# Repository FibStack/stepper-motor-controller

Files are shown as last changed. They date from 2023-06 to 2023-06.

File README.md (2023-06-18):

# Stepper Motor Controller

## Overview

This repository includes the source files for the Stepper Motor Control board, capable of controlling the direction, steps, and speed of up to four stepper motors concurrently through the I2C interface. 

Kindly note that the project is currently in the prototype phase, and further changes and updates are expected.

## Project organization

- **hardware/** - this folder contains the board circuit schematic and PCB design files.
- **software/util** - contains the source code of a simple CLI application to interact with the board.
- **software/stepper-motor-controller** - contains the firmware source code for ATTiny devices.

## Development tools
- **[Microchip Studio 7.0](https://www.microchip.com/en-us/tools-resources/develop/microchip-studio)**: The IDE for writing and building source code for the ATTiny chip. We also use this tool to flash the chip.
- **[ATMEL-ICE](https://www.microchip.com/en-us/development-tool/ATATMEL-ICE)**: Hardware tool for flashing program and EEPROM memories.
- **GCC** compiler: To complie C utility code on Raspberry Pi.
- **[KiCad EDA](https://www.kicad.org/)**: Schematic and PCB design.

To construct the PCB, please export the gerber files according to the manufacturer's guidelines.

To build the CLI utility, navigate to the `util` folder and execute the `make` command. Please note that this works only on **Raspberry Pi OS**.

To build the ATTiny826 firmware, open the project in Microchip Studio. Build the solution to generate the `*.HEX` and `*.EEP` files. Next, use the appropriate tool available to flash the chip.

## BOM

| # | Components | Recommended models | Footprint | Quantity |
| --- | --- | --- | --- | --- |
| 1 | PCB | Recommended two-layer PCB board of 1.6 mm thickness | | 1 |
| 2 | U1 | SN74LS148 | SOIC-16, 3.9x9.9mm, pitch: 1.27mm | 1 |
| 3 | U2 | ATtiny826 | SOIC-20, 7.5x12.8mm, pitch: 1.27mm | 1 |
| 4 | C1, C4 | Any 1uF 50V SMD capacitor | 0603 (1608 metric) | 2 |
| 5 | C2 | Any 10nF 50V SMD capacitor | 0603 (1608 metric) | 1 |
| 6 | C3, C5 | Any 100nF 50V SMD capacitor | 0603 (1608 metric) | 2 |
| 7 | R1 | Any 470 - 1K 5% 1/4W SMD Resistor | 0603 (1608 metric) | 1 |
| 8 | R2-R13 | Any 10K 5% 1/4W SMD Resistor | 0603 (1608 metric) | 12 |
| 9 | Q1, Q2 | 2N7002 N-channel MOSFET transistor, 60V 300mA | SOT-23-2 | 2 |
| 10 | D1 | SMD LED RED | 0603 (1608 metric) | 1 |
| 11 | J1 | Extended GPIO Male Female Header, 2x20, pitch 2.54mm | 2x20 - P2.54mm | 1 |
| 12 | J2 | Optional, Male Header Connector, 2x3, pitch 2.54mm | 2x3 - P2.54mm | 1 |
| 13 | J3 | Any male connector, 1x2, pitch 2.54mm | 1x2 - P2.54mm | 1 |
| 14 | J4 | Male Header Connector, 2x8, pitch 2.54mm | 2x8 - P2.54mm | 1 |
| 15 | J5, J6, J7, J8 | Male Header Connector, 1x4, pitch 2.54mm | 1x4 - P2.54mm | 4 |
| 16 | SW1 | SPDT 3-pin vertical slide switch | P2.54mm | 1 |

## Documentation

For more detailed information about the board and the I2C protocol, please visit the [project page](https://fibstack.com/projects/stepper-motor-controller/).

## License Information
This product is open source!

Please review the LICENSE.md file for license information. Distributed as-is; no warranty is given.

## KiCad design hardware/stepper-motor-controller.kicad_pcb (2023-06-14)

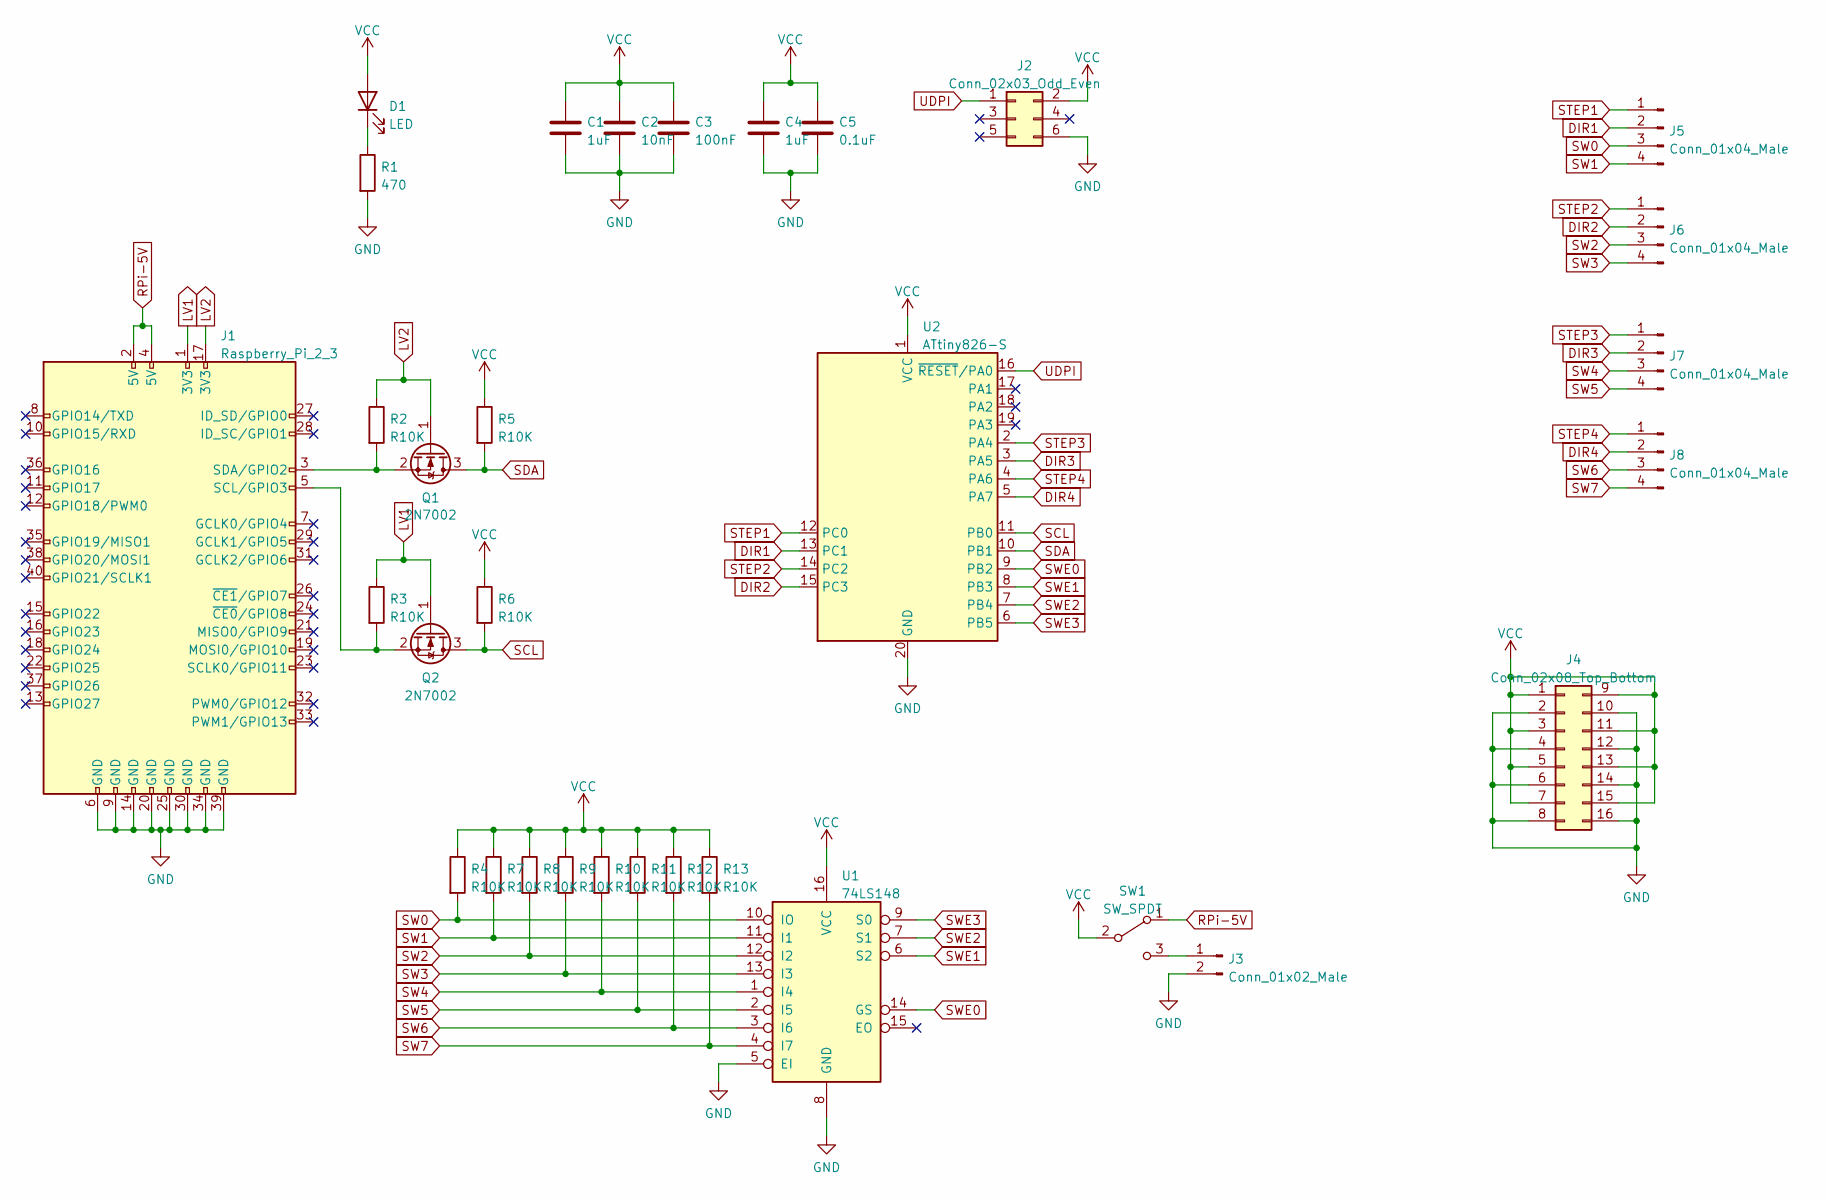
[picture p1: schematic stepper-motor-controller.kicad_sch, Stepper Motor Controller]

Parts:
C1, C4: 1uF; C_0603_1608Metric
C2: 10nF; C_0603_1608Metric
C3: 100nF; C_0603_1608Metric
C5: 0.1uF; C_0603_1608Metric
D1: LED; LED_0603_1608Metric
J1: Raspberry_Pi_2_3; PinHeader_2x20_P2.54mm_Vertical
J2: Conn_02x03_Odd_Even; PinHeader_2x03_P2.54mm_Vertical
J3: Conn_01x02_Male; PinHeader_1x02_P2.54mm_Vertical
J4: Conn_02x08_Top_Bottom; PinHeader_2x08_P2.54mm_Vertical
J5, J6, J7, J8: Conn_01x04_Male; PinHeader_1x04_P2.54mm_Vertical
Q1, Q2: 2N7002; SOT-23
R1: 470; R_0603_1608Metric
R2, R3, R4, R5, R6, R7, R8, R9, R10, R11, R12, R13: R10K; R_0603_1608Metric
SW1: SW_SPDT; PinHeader_1x03_P2.54mm_Vertical
U1: 74LS148; SOIC-16_3.9x9.9mm_P1.27mm
U2: ATtiny826-S; SOIC-20W_7.5x12.8mm_P1.27mm

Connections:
DIR1: J5.2, U2.13 (PC1)
DIR2: J6.2, U2.15 (PC3)
DIR3: J7.2, U2.3 (PA5)
DIR4: J8.2, U2.5 (PA7)
GND: C1.2, C2.2, C3.2, C4.2, C5.2, J1.6 (GND), J1.9 (GND), J1.14 (GND), J1.20 (GND), J1.25 (GND), J1.30 (GND), J1.34 (GND), J1.39 (GND), J2.6, J3.2, J4.2, J4.4, J4.6, J4.8, J4.10, J4.12, J4.14, J4.16, R1.2, U1.5 (EI), U1.8 (GND), U2.20 (GND)
LV1: J1.1 (3V3), Q2.1 (G), R3.1
LV2: J1.17 (3V3), Q1.1 (G), R2.1
unnamed: D1.1 (K), R1.1
unnamed: J1.3 (SDA/GPIO2), Q1.2 (S), R2.2
unnamed: J1.5 (SCL/GPIO3), Q2.2 (S), R3.2
unnamed: J3.1, SW1.3 (C)
RPi-5V: J1.2 (5V), J1.4 (5V), SW1.1 (A)
SCL: Q2.3 (D), R6.2, U2.11 (PB0)
SDA: Q1.3 (D), R5.2, U2.10 (PB1)
STEP1: J5.1, U2.12 (PC0)
STEP2: J6.1, U2.14 (PC2)
STEP3: J7.1, U2.2 (PA4)
STEP4: J8.1, U2.4 (PA6)
SW0: J5.3, R4.2, U1.10 (IO)
SW1: J5.4, R7.2, U1.11 (I1)
SW2: J6.3, R8.2, U1.12 (I2)
SW3: J6.4, R9.2, U1.13 (I3)
SW4: J7.3, R10.2, U1.1 (I4)
SW5: J7.4, R11.2, U1.2 (I5)
SW6: J8.3, R12.2, U1.3 (I6)
SW7: J8.4, R13.2, U1.4 (I7)
SWE0: U1.14 (GS), U2.9 (PB2)
SWE1: U1.6 (S2), U2.8 (PB3)
SWE2: U1.7 (S1), U2.7 (PB4)
SWE3: U1.9 (S0), U2.6 (PB5)
UDPI: J2.1, U2.16 (~RESET/PA0)
VCC: C1.1, C2.1, C3.1, C4.1, C5.1, D1.2 (A), J2.2, J4.1, J4.3, J4.5, J4.7, J4.9, J4.11, J4.13, J4.15, R4.1, R5.1, R6.1, R7.1, R8.1, R9.1, R10.1, R11.1, R12.1, R13.1, SW1.2 (B), U1.16 (VCC), U2.1 (VCC)

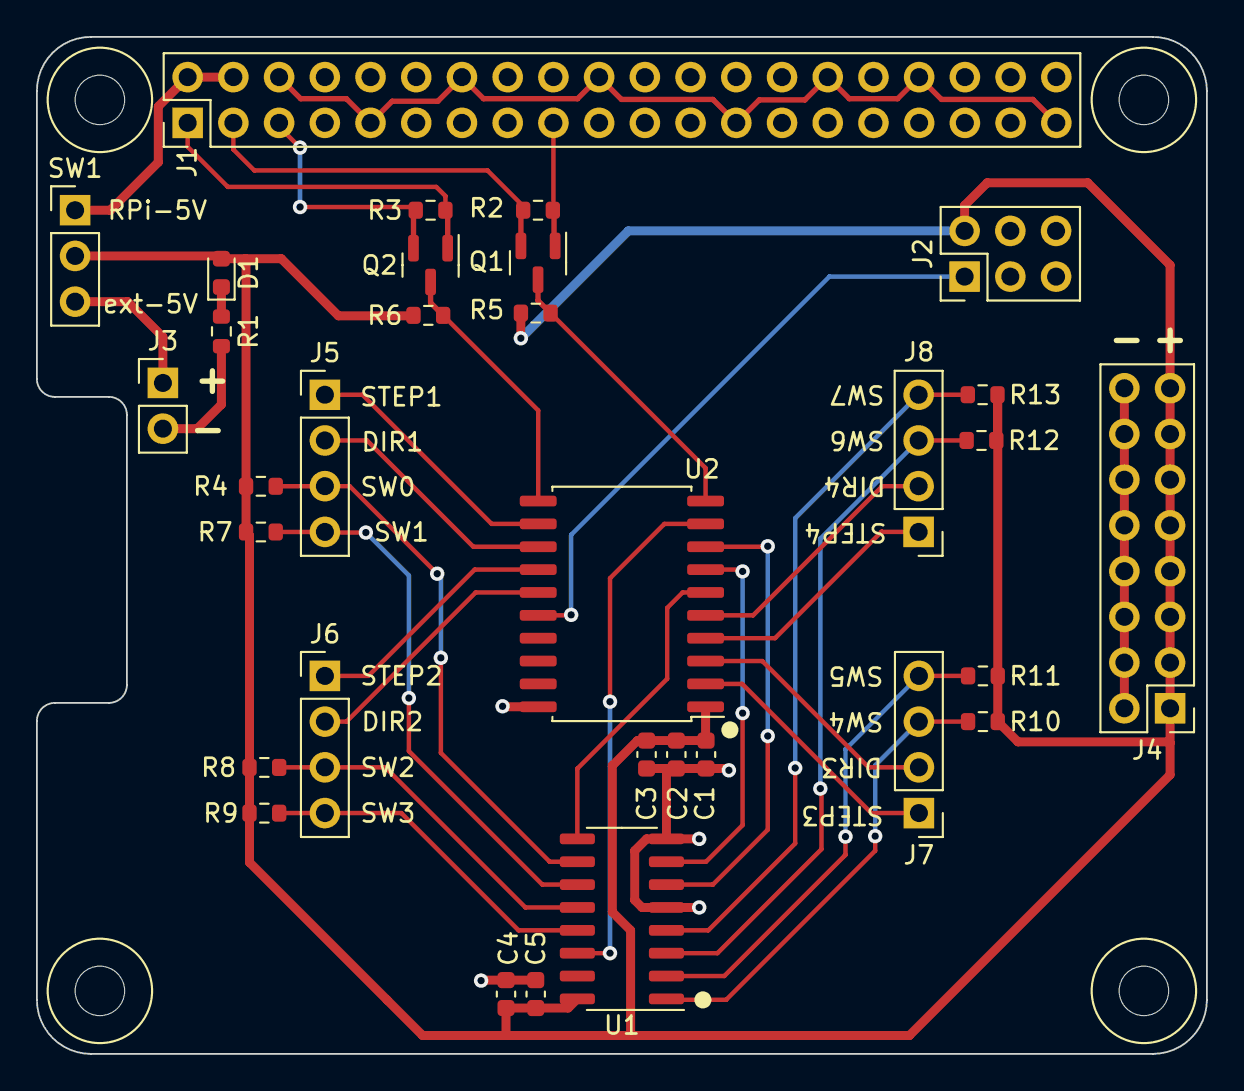
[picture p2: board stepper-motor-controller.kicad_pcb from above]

Board: 2 copper layers, 65.0 x 56.5 mm, 32 parts (0 on the bottom side), 32 nets.

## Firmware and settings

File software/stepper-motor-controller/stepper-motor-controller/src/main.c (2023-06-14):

/*
* Copyright (c) 2023, FibStack
* All rights reserved.
*
* This source code is licensed under the MIT license found in the
* LICENSE file in the root directory of this source tree.
*/

#include <avr/io.h>
#include <avr/interrupt.h>
#include <string.h>
#include "util.h"
#include "twi.h"
#include "tca.h"
#include "motors.h"

void PORTA_init();
void PORTC_init();

ISR(TWI0_TWIS_vect)
{
	// Processing receiving/sending data through I2C interface
	TWI0_process_interrupt();
}

ISR(TCA0_OVF_vect)
{
	// Processing commands at each TimerA overflow
	
	if(!is_switch_activated && !is_paused && move_device_id == MOTOR_DEVICES) {
		// No switch is activated, commands are not paused, and no override move command, run commands from the buffer
		run_command_on_device(&runCommnadsBufferA[head], 0);
		run_command_on_device(&runCommnadsBufferB[head], 1);
		run_command_on_device(&runCommnadsBufferC[head], 2);
		run_command_on_device(&runCommnadsBufferD[head], 3);
		
		if(!is_buffer_command_available(head)) {
			// No remaining steps, clear the other values from the buffer
			clear_command_struct(&runCommnadsBufferA[head]);
			clear_command_struct(&runCommnadsBufferB[head]);
			clear_command_struct(&runCommnadsBufferC[head]);
			clear_command_struct(&runCommnadsBufferD[head]);
			// Move to the next command if available
			uint8_t next_command_index = (head + 1) % COMMAND_BUFFER_SIZE;
			if(is_buffer_command_available(next_command_index)) {
				head = next_command_index;
			}
		}
	}
	else if (move_device_id < MOTOR_DEVICES && moveCommand.steps > 0)
	{
		// Execute move command, takes precedence over commands in the buffer
		run_command_on_device(&moveCommand, move_device_id);
	}
	else if (move_device_id < MOTOR_DEVICES && moveCommand.steps == 0)
	{
		// Reset move command
		clear_command_struct(&moveCommand);
		move_device_id = MOTOR_DEVICES;
		// Update if any switches are activated
		is_switch_activated = !((PORTB.IN >> 2) == 15);
		// Pause running commands, user must send resume command
		is_paused = 1;
	}
	
	// Stop if any of the limit switches are activated
	if((PORTB.IN >> 2) != 15)
	{
		is_switch_activated = 1;
	}
	
	TCA0.SINGLE.INTFLAGS = TCA_SINGLE_OVF_bm;
}

int main(void)
{
	uint8_t twi_address = eeprom_read_byte(&eeprom_twi_address);
	TWI0_init(twi_address);
	PORTA_init();
	PORTC_init();
	TCA0_init();
	clear_command_buffer();
	sei();
	
	while(1)
	{
		// Program loop
	}
}

void PORTC_init()
{
	// Configure physical pins 12, 13, 14, and 15 as output.
	PORTC.DIR |= PIN0_bm | PIN1_bm | PIN2_bm | PIN3_bm;
	PORTC.OUT |= PIN0_bm | PIN1_bm | PIN2_bm | PIN3_bm;
}

void PORTA_init()
{
	// Configure physical pins 2, 3, 4, and 5 as output.
	PORTA.DIR |= PIN4_bm | PIN5_bm | PIN6_bm | PIN7_bm;
	PORTA.OUT |= PIN4_bm | PIN5_bm | PIN6_bm | PIN7_bm;
}

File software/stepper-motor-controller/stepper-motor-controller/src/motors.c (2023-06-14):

/*
* Copyright (c) 2023, FibStack
* All rights reserved.
*
* This source code is licensed under the MIT license found in the
* LICENSE file in the root directory of this source tree.
*/


#include <avr/io.h>
#include "motors.h"

uint8_t head = 0;
uint8_t tail = 0;

// Buffers to store commands for each device
RunCommand runCommnadsBufferA[COMMAND_BUFFER_SIZE];
RunCommand runCommnadsBufferB[COMMAND_BUFFER_SIZE];
RunCommand runCommnadsBufferC[COMMAND_BUFFER_SIZE];
RunCommand runCommnadsBufferD[COMMAND_BUFFER_SIZE];

// Predefined ports and mask for each motor
PORT_t* device_ports[MOTOR_DEVICES] = {&PORTC, &PORTC, &PORTA, &PORTA};
uint8_t device_step_masks[MOTOR_DEVICES] = {PIN0_bm, PIN2_bm, PIN4_bm, PIN6_bm};
uint8_t device_dir_masks[MOTOR_DEVICES] = {PIN1_bm, PIN3_bm, PIN5_bm, PIN7_bm};
	
uint8_t is_switch_activated = 0; // Indicates that a limit switch is activated
uint8_t is_paused = 0; // Indicates if commands are paused or not

// Special move command
RunCommand moveCommand = {0, 0, 0, 0};
uint8_t move_device_id = MOTOR_DEVICES;

/**
* Helper function to clear a command
*/
void clear_command_struct(RunCommand* run_command)
{
	run_command->steps = 0;
	run_command->dir = 0;
	run_command->speed = 0;
	run_command->counter = 0;
}

/**
* Helper function to clear all the commands in the buffer
*/
void clear_command_buffer()
{
	for(int i = 0; i < COMMAND_BUFFER_SIZE; i++) {
		clear_command_struct(&runCommnadsBufferA[i]);
		clear_command_struct(&runCommnadsBufferB[i]);
		clear_command_struct(&runCommnadsBufferC[i]);
		clear_command_struct(&runCommnadsBufferD[i]);
	}
}

/**
* Runs one steps from the command
*/
void run_command_on_device(RunCommand* run_command, uint8_t device_id)
{
	// Skip if no steps to run
	if(run_command->steps == 0) {
		return;
	}
	
	run_command->counter++;
	
	if(run_command->counter >= run_command->speed) {
		
		// Set direction
		if(run_command->dir)
		{
			device_ports[device_id]->OUT |= device_dir_masks[device_id];
		}
		else
		{
			device_ports[device_id]->OUT &= ~device_dir_masks[device_id];
		}
		// Toggle step pin
		device_ports[device_id]->OUT ^= device_step_masks[device_id]; // toggle step pin
		if((device_ports[device_id]->OUT & device_step_masks[device_id]) == 0) {
			run_command->steps--;
		}
		run_command->counter = 0;
	}
}

/**
* Helper function to check if there is a command with steps to be executed.
*/
uint8_t is_buffer_command_available(uint8_t index)
{
	if (index >= COMMAND_BUFFER_SIZE)
	{
		return 0;
	}
	
	return runCommnadsBufferA[index].steps > 0 || runCommnadsBufferB[index].steps > 0 ||
		runCommnadsBufferC[index].steps > 0 || runCommnadsBufferD[index].steps > 0;
}

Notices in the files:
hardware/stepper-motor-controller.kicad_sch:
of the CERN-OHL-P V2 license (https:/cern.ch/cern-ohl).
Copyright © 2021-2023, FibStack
